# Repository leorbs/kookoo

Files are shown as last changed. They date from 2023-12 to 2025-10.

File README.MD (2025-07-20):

## KOOKOO
~~Very simple~~ script to control a Cuckoo, multiple sensors and sound playback.

## Connecting
Most of the cables have color codes at the end. If you are unsure, read 
the schematics or board layout.

## Compiling

Follow the instructions in the script.ino. When compiling, choose the old bootloader
for the arduino nano:

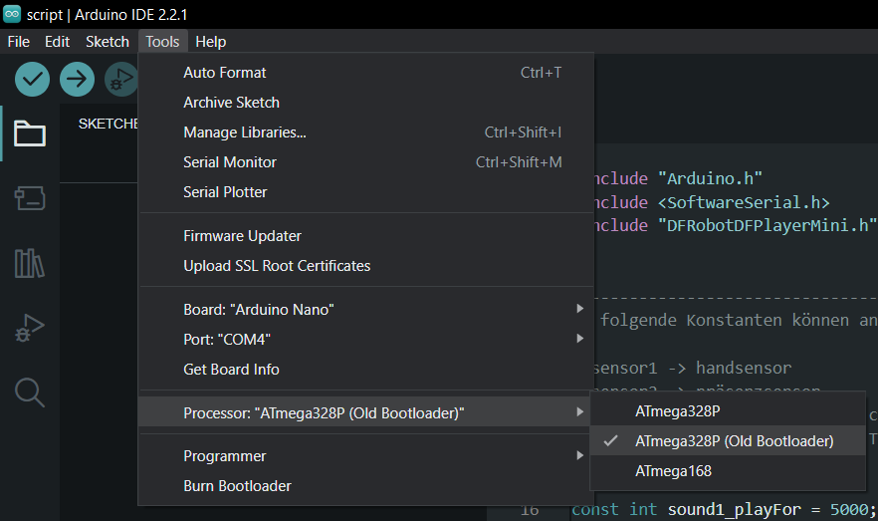
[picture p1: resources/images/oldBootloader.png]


## How to use the SD card

follow the instructions [here](/resources/folderStructure.MD)

## Troubleshooting

- Hand sensor does not work
  - look inside and observe the leds. The LED of the hand sensor module 
  and the LED of the Arduino should light up, when something is near the sensor 
    -  if there is no change on the LEDs then you can try to 
    lower the sensitivity of the sensor module. Look into the guide of
    the sensor module
    - there might be too much sunlight hitting the IR sensor. Try blocking the 
    sunlight and test if the sensor works again
- Shake logic to sensitive
  - adjust values in code
    - SHAKE_SENSITIVITY
    - SHAKE_PICKUP_SPEED
    - SHAKE_OBSERVATION_WINDOW

## PCB Layout
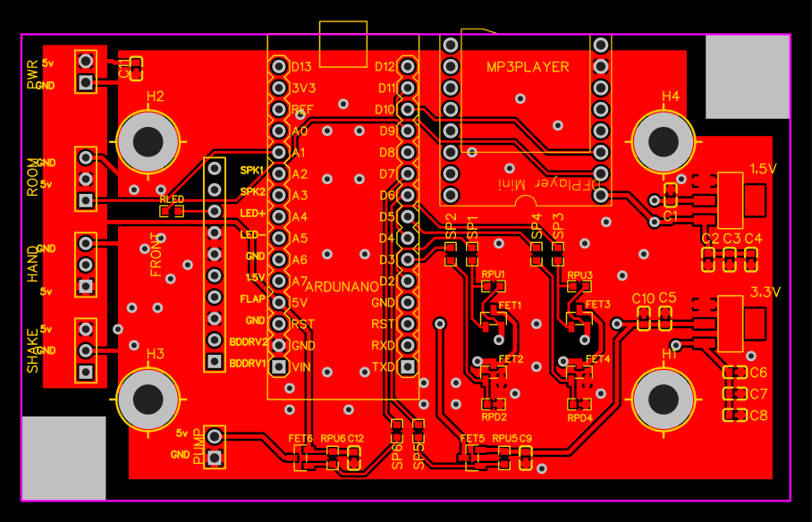
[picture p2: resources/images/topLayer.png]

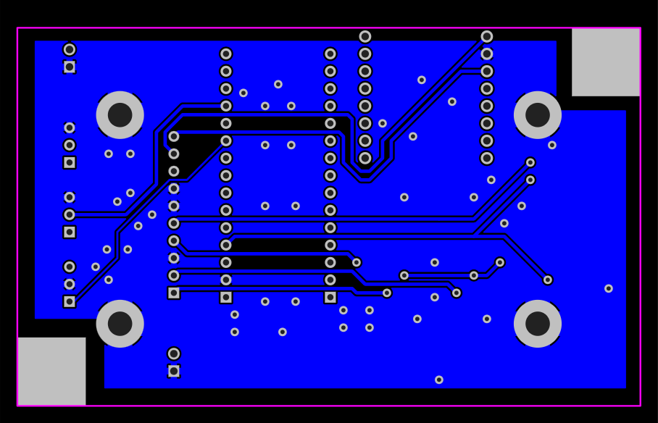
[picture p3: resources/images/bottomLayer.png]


### PCB Schematic

*Mandatory* needs to be fixed directly on the PCB (for now).

- change the resistor if you want a brighter LED
- add a schotty diode to the flap

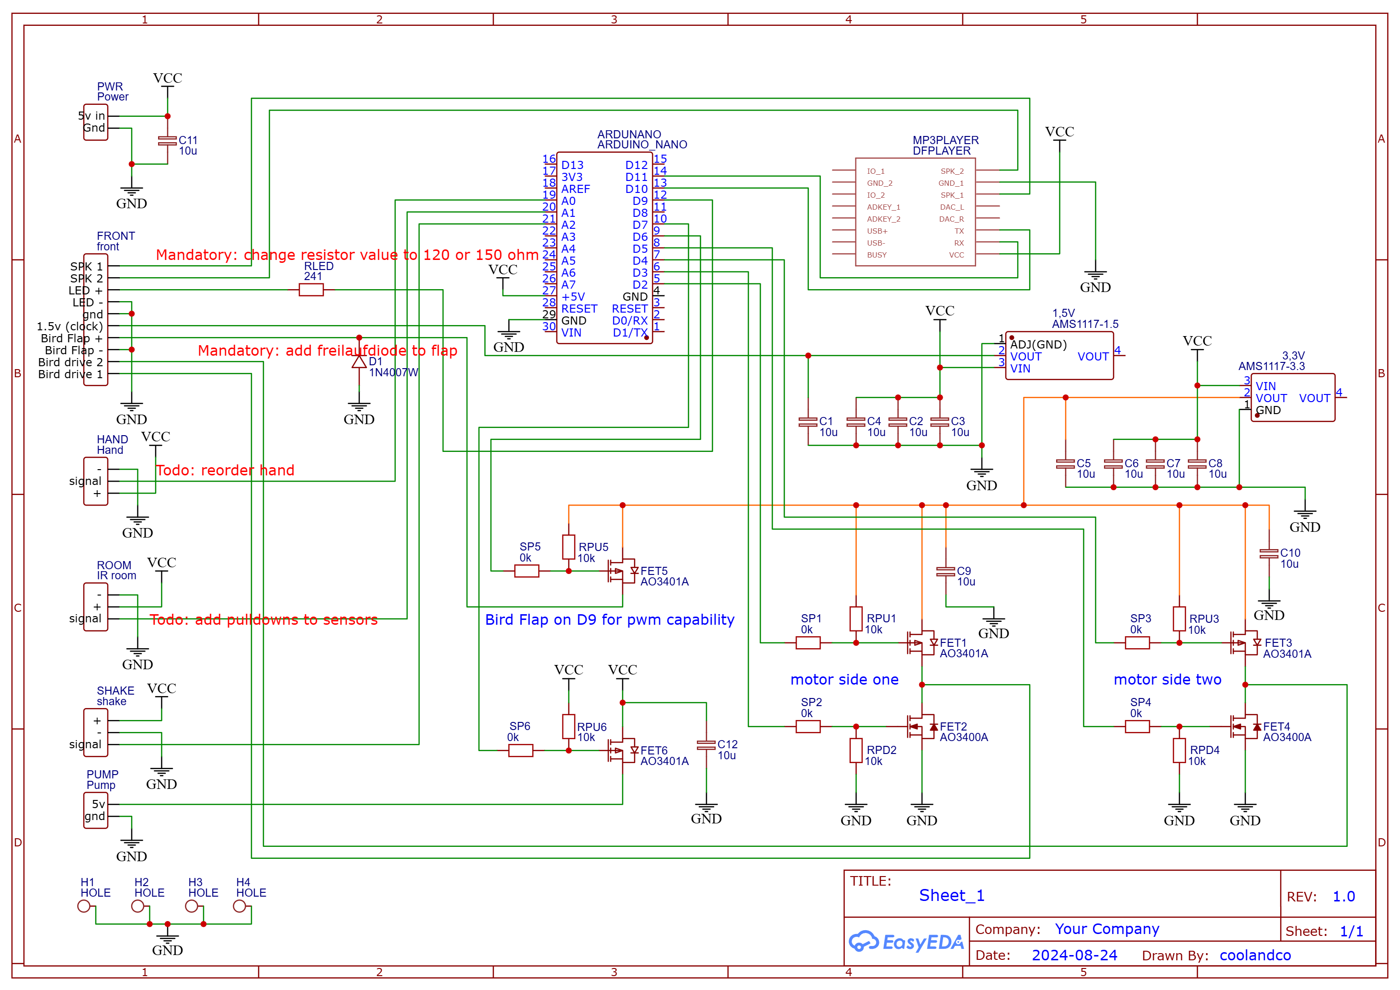
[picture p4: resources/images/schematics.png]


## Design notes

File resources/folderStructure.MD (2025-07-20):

##
Format the MicroUSB in Fat32, standard allocation.
Partitioning table should be in MBR (to be verified).
## Files

Use only files with codecs that the DFPlayer Chip can play. 

One known working solution is the following:
- Open Audacity and mark a section you want to export.
- Press STRG + Shift + E (Export Audio)
  - Format: WAV (Microsoft)
  - Channels: Mono
  - Sample Rate: 44100Hz
  - Encoding: Signed 16-bit PCM
- Export Range: current section
- Export!

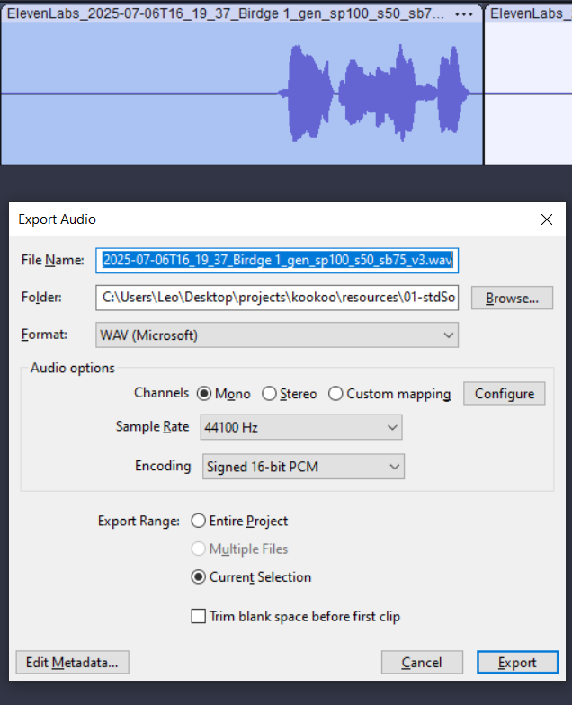
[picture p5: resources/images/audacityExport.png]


## Folder Structure

Example folder names: 
- ``03/001.mp3``
- ``03/002.mp3``
- ``03/003.mp3``
- ``04/001.mp3``

Folder name: only two digits ``01`` - ``13``

File name: three digits + ending e.g.: ``001.wav``. The ending can be wav or mp3.

If a folder is not used anymore, delete that folder (no empty folders)!
If you see a ``System Volume Information`` folder, dont bother, it can stay.

### Folder meaning:
- 01
  - Kookoo standard bird sound(s)
- 02
  - shake sensor activated sounds
- 03
  - one file: 001.wav
  - for the menu beep
- 04 - 13
  - 'someone comes into the room' sounds
  - press the button to iterate through these folders
  - one beep -> folder 04
  - two beeps -> folder 05
  - ...

## Note to the code developer: How does the detection of files work?
Detection of folders works by calling ``mp3Player.readFolderCounts();`` several times
and comparing if the results are the same for multiple consecutive times.
The chip detects folders with files in them.

Detection of files work by playing the first file from a folder and then asking the
chip to return the amount of files from that Folder ``mp3Player.readFileCountsInFolder(i);``.
The amount of files is requested multiple times and after multiple consecutive same answers
it is taken as correct.

Somehow this reliably works. I dont know why...

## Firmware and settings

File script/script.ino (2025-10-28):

#include "Arduino.h"
#include "SoftwareSerial.h"
#include "DFRobotDFPlayerMini.h"
#include "JobManager.cpp"
#include "TimeBasedCounter.cpp"
#include "BirdFlapGenerator.h"
#include "Bounce2.h"

//----------------------------------------
//Install the following libraries from your arduino library manager
//https://github.com/thomasfredericks/Bounce2
//https://github.com/end2endzone/SoftTimers

// use the old bootloader for arduino nano when compiling


// uncomment this line, if you want to show logs on serial:

// #define DEBUG
//----------------------------------------
// Settings

#define VOLUME 23                         // sound volume 0-30

#define SHAKE_SENSITIVITY 20              // up to 1024. The higher the number, the lower the sensitivity
#define SHAKE_PICKUP_SPEED 150            // minimum time in ms between shake incidents to get registered
#define SHAKE_OBSERVATION_WINDOW 4000     // Window to observe shakes in ms
#define COUNTER_SIZE 3                    // how many times should the sensor detect a shake within the window 
#define SHAKE_DETECTION_TIMEOUT 10000     // how much time after the last shake execution (Pfoten weg) before the shake sensor is active again (ms)?

#define ROOM_DETECTION_TIMEOUT 60000      // how much time after the last activity before the room sensor is active (ms)?


#define LED1_BRIGHTNESS 255      // 0-255 led from the front header (big connector)
#define LED2_BRIGHTNESS 255      // 0-255  

#define SOAP_AMOUNT 350          // How long is the Pump on (ms)?
#define LED_BLINKING_SPEED 500   // How long is the LED on/off (ms), Blinking speed.


//----------------------------------------
// internals

#define MAIN_LOOP_TIME_BASE_MS	5

#define HAND_PIN A0            // connect IR hand sensor module to Arduino pin A0
#define ROOM_PIN A1            // praesense sensor module to Arduino pin A1
#define SHAKE_PIN A2           // sensor module for tamper detection to Arduino pin A2

#define RNG_SEED_PIN A6        // Used to initialize the randomnes

#define BUTTON_1 12            // Button for setting the folder
#define BUTTON_2 A3            // Button for setting the folder
#define BUTTON_3 A5            // Button for manual soap

#define LED1_PIN 9             // D9 LED
#define LED2_PIN A4            // LED2
#define PUMP_PIN 7             // D7 soap pump

#define BIRD_FLAP_PIN 6        // D6 bird flap

#define BIRD_MOTOR1_GND_PIN 5  // D5 
#define BIRD_MOTOR1_VCC_PIN 2  // D2

#define BIRD_MOTOR2_GND_PIN 3  // D3 
#define BIRD_MOTOR2_VCC_PIN 4  // D4

#define DFPLAYER_RX_PIN 10     // D10 -> RX on Arduino TX on DFPlayer
#define DFPLAYER_TX_PIN 11     // D11 -> TX on Arduino RX on DFPlayer



#ifdef DEBUG
  #warning "Serial debugging is enable. This will slow down program flow"
#endif


// DFPlayer maintenance timers
unsigned long lastDFPlayerReset = 0;
unsigned long lastSoapUse = 0;

// Intervals
const unsigned long DFPLAYER_RESET_INTERVAL = 10UL * 24UL * 60UL * 60UL * 1000UL; // 10 days
const unsigned long INACTIVITY_WINDOW = 3UL * 60UL * 60UL * 1000UL;               // 3 hours

SoftwareSerial DFPlayerSoftwareSerial(DFPLAYER_RX_PIN,DFPLAYER_TX_PIN);// RX, TX
DFRobotDFPlayerMini mp3Player;
SoftTimer mainLoopTimer;

#define FOLDER_STANDARD_BIRD_SOUND 1
#define FOLDER_SHAKE_SENSOR_ACTIVATED 2
#define FOLDER_BEEP 3
#define FOLDER_ROOM_START 4
#define FOLDER_ROOM_END 13

uint8_t maxDetectedFolders = FOLDER_ROOM_END;
uint8_t folderFileCounts[FOLDER_ROOM_END + 1]; // Index 1-13 used
uint8_t currentRoomFolder = FOLDER_ROOM_START;
uint8_t currentRoomFolder_beepCyclePosition = 0;

Bounce2::Button button1 = Bounce2::Button();
Bounce2::Button button2 = Bounce2::Button();
Bounce2::Button button3 = Bounce2::Button();


TimeBasedCounter timeBasedCounter(SHAKE_OBSERVATION_WINDOW);
unsigned long currentTime = 0;

void soundOn();
void soundOff();
void flapStart();
void flapEnd();
void birdOutStart();
void birdOutEnd();
void birdInStart();
void birdInEnd();
void flapBreakStart();
void flapBreakEnd();
void soapOn();
void soapOff();
void roomOn();
void roomOff();
void shakeOn();
void shakeOff();
void ledOnStart();
void ledOnEnd();
void ledOffStart();
void ledOffEnd();
void doMp3PlayerSetupStuff();

const uint16_t flapBreakPattern_single[] = {200, 600};
const uint16_t flapPattern_single[] =        {500};

SoundParams soundParams;

int flapPattern_currentIndex = 0;
int flapBreakPattern_currentIndex = 0;

JobManager sound(15000, 800, soundOn, soundOff, false, false); //backoff is the safety time for bird termination

JobManager flap(500, flapStart, flapEnd);
JobManager flapBreak(200, flapBreakStart, flapBreakEnd);
JobManager birdOut(240, birdOutStart, birdOutEnd);
JobManager birdIn(260, birdInStart, birdInEnd);

JobManager soap(SOAP_AMOUNT, 2000, soapOn, soapOff, true, true);
JobManager room(500, ROOM_DETECTION_TIMEOUT, roomOn, roomOff, true, true);
JobManager shake(550, 10000, shakeOn, shakeOff, false, true);

// only sound will control bird
// bird can only come out with sound
// that means if one sound is running, there can be no other sound and therefore no other bird
// sound execution time -> full bird cycle. Execution time mandatory to prevent double bird scenario

JobManager ledOn(LED_BLINKING_SPEED, ledOnStart, ledOnEnd);
JobManager ledOff(LED_BLINKING_SPEED, ledOffStart, ledOffEnd);


void soapOn() {
  Serial.println(F("switch soap on"));
  digitalWrite(PUMP_PIN, LOW);

  // set new sound params for the sound job
  Serial.print(sound.isJobActive());
  Serial.println(F(" = Sound job currently active"));

  if(!sound.isJobActive()) {

    soundParams.folderId = FOLDER_STANDARD_BIRD_SOUND;
    soundParams.triggerBird = true;
    Serial.print(F(" setting soundParams.flapBreakPattern. flapBreakPattern_single[0]: "));
    Serial.println(flapBreakPattern_single[0]);
    soundParams.flapBreakPattern = flapBreakPattern_single;
    soundParams.flapPattern = flapPattern_single;
    soundParams.flapBreakPatternSize = 2;
    soundParams.flapPatternSize = 1;

    sound.startJob();
  }

}

void soapOff() {
  Serial.println(F("switch soap off"));
  digitalWrite(PUMP_PIN, HIGH);
}

void roomOn() {

  Serial.println(F("room On"));

  if(!sound.isJobActive()) {
    //execute the chain
    generateSpeechLikeFlappingPattern(soundParams);
    soundParams.folderId = currentRoomFolder;
    soundParams.triggerBird = true;

    sound.startJob();
  }
}

void roomOff() {
}

void shakeOn() {
  Serial.println(F("shake On"));
  if(!sound.isJobActive()) {

    // flaps get ignored because trigger bird is false
    soundParams.folderId = FOLDER_SHAKE_SENSOR_ACTIVATED;
    soundParams.triggerBird = false;
    soundParams.flapBreakPattern = flapBreakPattern_single;
    soundParams.flapPattern = flapPattern_single;
    soundParams.flapBreakPatternSize = 2;
    soundParams.flapPatternSize = 1;

    //execute the chain
    sound.startJob();
  }
}

void shakeOff() {
}

void soundOn() {

  Serial.println(F("sound on."));
  Serial.print(soundParams.folderId);
  Serial.println(F(" folderId playing"));

  
  int count = folderFileCounts[soundParams.folderId];
  uint8_t fileNum = random(1, count + 1);
  Serial.print(F("Playing file "));
  Serial.print(fileNum);
  Serial.print(F(" from folder "));
  Serial.println(soundParams.folderId);
  mp3Player.playFolder(soundParams.folderId, fileNum);

  if(soundParams.triggerBird) {
    Serial.println(F("Sound doing Birdstuff"));

    // 15 Seconds max sound lengh for safety
    // some other routine should test if mp3 is still playing and  stop sound job (and therefore pull in bird)
    sound.setNewDurationTime(15000);
    sound.restartJobTimer();

    flapPattern_currentIndex = 0;
    flapBreakPattern_currentIndex = 0;

    //execute the bird chain
    birdOut.startJob();
  }

}

void soundOff() {
}

void birdOutStart() {
  Serial.println(F("Bird out start"));
  digitalWrite(BIRD_MOTOR1_GND_PIN, HIGH);
  digitalWrite(BIRD_MOTOR1_VCC_PIN, LOW);
}

void birdOutEnd() {
  Serial.println(F("Bird out end"));
  digitalWrite(BIRD_MOTOR1_GND_PIN, LOW);
  digitalWrite(BIRD_MOTOR1_VCC_PIN, HIGH);
  
  //execute the chain
  if(soundParams.flapBreakPatternSize > soundParams.flapPatternSize) {
    flapBreak.startJob();
  } else {
    flap.startJob();
  }

}

void birdInStart() {
  Serial.println(F("Bird in start"));
  digitalWrite(BIRD_MOTOR2_GND_PIN, HIGH);
  digitalWrite(BIRD_MOTOR2_VCC_PIN, LOW);

}

void birdInEnd() {
  Serial.println(F("Bird in end"));
  digitalWrite(BIRD_MOTOR2_GND_PIN, LOW);
  digitalWrite(BIRD_MOTOR2_VCC_PIN, HIGH);
}


// ========================================================================================================================

void flapStart() {
  Serial.print(F("flap Start"));
  Serial.println(soundParams.flapPattern[flapPattern_currentIndex]);

  digitalWrite(BIRD_FLAP_PIN, LOW);

  flap.setNewDurationTime(soundParams.flapPattern[flapPattern_currentIndex]);
  flap.restartJobTimer();
}

void flapEnd() {
  Serial.println(F("flap End"));
  digitalWrite(BIRD_FLAP_PIN, HIGH);

  flapPattern_currentIndex = flapPattern_currentIndex + 1;

  //check flap break possible
  if(flapBreakPattern_currentIndex < soundParams.flapBreakPatternSize && sound.isJobActive()) {
    flapBreak.startJob();
  } else {
    //no flap break anymore (or sound got ended). Do now bird in
    birdIn.startJob();
  }

}

void flapBreakStart(){
  Serial.print(F("flapBreakStart "));
  Serial.println(soundParams.flapBreakPattern[flapBreakPattern_currentIndex]);

  flapBreak.setNewDurationTime(soundParams.flapBreakPattern[flapBreakPattern_currentIndex]);
  flapBreak.restartJobTimer();

}

void flapBreakEnd() {
  Serial.println(F("flapBreakEnd"));

  flapBreakPattern_currentIndex = flapBreakPattern_currentIndex + 1;


  //check flap possible
  if(flapPattern_currentIndex < soundParams.flapPatternSize && sound.isJobActive()) {
    flap.startJob();
  } else {
    //no flap anymore (or sound got ended). Do now bird in
    birdIn.startJob();
  }

}

// ========================================================================================================================
void printDetail(uint8_t type, int value){
  switch (type) {
    case TimeOut:
      Serial.println(F("DFPLAYER: Time Out!"));
      break;
    case WrongStack:
      Serial.println(F("DFPLAYER: Stack Wrong!"));
      break;
    case DFPlayerCardInserted:
      Serial.println(F("DFPLAYER: Card Inserted!"));
      break;
    case DFPlayerCardRemoved:
      Serial.println(F("DFPLAYER: Card Removed!"));
      break;
    case DFPlayerCardOnline:
      Serial.println(F("DFPLAYER: Card Online!"));
      break;
    case DFPlayerUSBInserted:
      Serial.println(F("DFPLAYER: USB Inserted!"));
      break;
    case DFPlayerUSBRemoved:
      Serial.println(F("DFPLAYER: USB Removed!"));
      break;
    case DFPlayerPlayFinished:
      Serial.print(F("DFPLAYER: Number: "));
      Serial.print(value);
      Serial.println(F(" Play Finished!"));
      break;
    case DFPlayerError:
      Serial.print(F("DFPLAYER: DFPlayerError:"));
      switch (value) {
        case Busy:
          Serial.println(F("DFPLAYER: Card not found"));
          break;
        case Sleeping:
          Serial.println(F("DFPLAYER: Sleeping"));
          break;
        case SerialWrongStack:
          Serial.println(F("DFPLAYER: Get Wrong Stack"));
          break;
        case CheckSumNotMatch:
          Serial.println(F("DFPLAYER: Check Sum Not Match"));
          break;
        case FileIndexOut:
          Serial.println(F("DFPLAYER: File Index Out of Bound"));
          break;
        case FileMismatch:
          Serial.println(F("DFPLAYER: Cannot Find File"));
          break;
        case Advertise:
          Serial.println(F("DFPLAYER: In Advertise"));
          break;
        default:
          break;
      }
      break;
    default:
      break;
  }
}

void setup() {
  mainLoopTimer.setTimeOutTime(MAIN_LOOP_TIME_BASE_MS);
  mainLoopTimer.reset();

  pinMode(HAND_PIN, INPUT_PULLUP);
  pinMode(ROOM_PIN, INPUT_PULLUP);
  pinMode(SHAKE_PIN, INPUT);

  pinMode(LED_BUILTIN, OUTPUT);
  pinMode(LED1_PIN, OUTPUT);

  pinMode(PUMP_PIN, OUTPUT);
  digitalWrite(PUMP_PIN, HIGH);

  pinMode(BIRD_FLAP_PIN, OUTPUT);
  digitalWrite(BIRD_FLAP_PIN, HIGH);

  pinMode(BIRD_MOTOR1_GND_PIN, OUTPUT);
  digitalWrite(BIRD_MOTOR1_GND_PIN, LOW);
  pinMode(BIRD_MOTOR1_VCC_PIN, OUTPUT);
  digitalWrite(BIRD_MOTOR1_VCC_PIN, HIGH);
  pinMode(BIRD_MOTOR2_GND_PIN, OUTPUT);
  digitalWrite(BIRD_MOTOR2_GND_PIN, LOW);
  pinMode(BIRD_MOTOR2_VCC_PIN, OUTPUT);
  digitalWrite(BIRD_MOTOR2_VCC_PIN, HIGH); 

  button1.attach ( BUTTON_1 , INPUT_PULLUP );
  button1.interval( 10 );
  button1.setPressedState( LOW );

  button2.attach ( BUTTON_2 , INPUT_PULLUP );
  button2.interval( 10 );
  button2.setPressedState( LOW );

  button3.attach ( BUTTON_3 , INPUT_PULLUP );
  button3.interval( 10 );
  button3.setPressedState( LOW );


  #ifdef DEBUG
    Serial.begin(9600);
  #endif

  int seed = analogRead(RNG_SEED_PIN);

  Serial.print(F("seed is: "));
  Serial.println(seed);

  //initialize randomness so it is not every time the same
  randomSeed(seed);



  //mp3 player stuff
  DFPlayerSoftwareSerial.begin(9600); // DFPlayer Mini mit SoftwareSerial initialisieren
  bool mp3PlayerOnline = mp3Player.begin(DFPlayerSoftwareSerial, true, true);
  
  if(mp3PlayerOnline) {
    doMp3PlayerSetupStuff();
  }


  ledOn.startJob();
}

void doMp3PlayerSetupStuff() {
  mp3Player.setTimeOut(2000);
  mp3Player.volume(0);
  delay(50);

  int consecutiveSame = 0;
  int lastValue = INT16_MAX;
  int currentRead;
  bool filedetection = false;


  while(consecutiveSame < 4) {
    Serial.print(F("consecutiveSame: "));
    Serial.println(consecutiveSame);
    currentRead = mp3Player.readFolderCounts();

    if(mp3Player.available() ) {
        uint8_t type = mp3Player.readType();
        int value = mp3Player.read();
        printDetail(type, value);
    }
    Serial.print(F("currentRead: "));
    Serial.println(currentRead);
    if(lastValue == currentRead){
      consecutiveSame += 1;
    } else {
      consecutiveSame = 0;
      lastValue = currentRead;
    }
  }

  maxDetectedFolders = lastValue;
  Serial.print(F("maxDetectedFolders after readFolderCounts "));
  Serial.println(maxDetectedFolders);

  if(maxDetectedFolders > FOLDER_ROOM_END || maxDetectedFolders < 0) {

    Serial.print(F("Getting folder count is not supported or errornous. Falling back to file detection "));
    filedetection = true;

    maxDetectedFolders = FOLDER_ROOM_END; //setting temporary for iterating over folders (this is not good code, I know, sry)
  }

  for (int i = 1; i <= maxDetectedFolders; i++) {
    mp3Player.playFolder(i, 1);
    delay(100);

    lastValue = INT16_MAX;
    consecutiveSame = 0;
    while(consecutiveSame < 6) {
      Serial.print(F("consecutiveSame: "));
      Serial.println(consecutiveSame);
      currentRead = mp3Player.readFileCountsInFolder(i);
      
      if(mp3Player.available() ) {
        uint8_t type = mp3Player.readType();
        int value = mp3Player.read();
        printDetail(type, value);
      }

      delay(50);
      Serial.print(F("currentRead: "));
      Serial.println(currentRead);
      if(lastValue == currentRead){
        consecutiveSame += 1;
      } else {
        consecutiveSame = 0;
        lastValue = currentRead;
      }
    }

    // mp3Player.playFolder(i, lastValue);
    // delay(100);
    // currentRead = mp3Player.readFileCountsInFolder(i);
    // Serial.print(F("lastValue currentRead: "));
    // Serial.println(currentRead);

    folderFileCounts[i] = lastValue;

    Serial.print(F("folderFileCounts[i] i: "));
    Serial.print(i);
    Serial.print(F(" folderFileCounts: "));
    Serial.println(lastValue);

    if(lastValue == 0) {
      Serial.println(F("Found a Folder with 0 files. Aborting... "));
      break;
    } else if (lastValue == -1) {
      Serial.println(F("Found a Folder with -1 files. Aborting... "));
      break;
    }
  }


  if(filedetection) {
    Serial.println(F("Filedetection is active."));
    maxDetectedFolders = 0;

    for(int i = 1; i <= FOLDER_ROOM_END; i++) {
      if(folderFileCounts[i] > 0 && folderFileCounts[i] < 255) {
        maxDetectedFolders = maxDetectedFolders + 1;
      } else {
        //abort when there is a folder detected with 0 files
        break;
      }
    }

    Serial.print(F("Detected files in the first X folders: "));
    Serial.println(maxDetectedFolders);

    if(maxDetectedFolders > FOLDER_ROOM_END) {
      //safety
      maxDetectedFolders = FOLDER_ROOM_END;
      Serial.println(F("Safety for filedetection activated"));
    }
  }


  mp3Player.stop();
  delay(500);

  mp3Player.volume(VOLUME);
  mp3Player.setTimeOut(1000);
}

void reinitializeDFPlayerSerial() {

  mp3Player.stop();
  delay(200);

  DFPlayerSoftwareSerial.end();
  delay(100);

  DFPlayerSoftwareSerial.begin(9600);
  delay(200);

  bool ok = mp3Player.begin(DFPlayerSoftwareSerial, true, true);

  Serial.println(F("Reinitialized MP3 Player"));
  if (ok) {
  Serial.println(F("initialization was ok"));
    mp3Player.volume(VOLUME);
  }
  
}


void loop() {
  while(!mainLoopTimer.hasTimedOut());
  mainLoopTimer.reset();
  
  currentTime = millis();

  // Sensor-Zustand überprüfen
  bool handSensor_isOn = !digitalRead(HAND_PIN);
  bool roomSensor_isOn = digitalRead(ROOM_PIN);
  uint16_t shakeSensor_value = analogRead(SHAKE_PIN);

  //display sensor1 state with buldin led
  digitalWrite(LED_BUILTIN, handSensor_isOn);

  button1.update();
  button2.update();
  button3.update();

  soap.handleJob();
  room.handleJob();
  shake.handleJob();
  sound.handleJob();
  birdOut.handleJob();
  birdIn.handleJob();
  flap.handleJob();
  flapBreak.handleJob();
  ledOn.handleJob();
  ledOff.handleJob();


  //--------------------------------------
  // sound observation loop

  if(mp3Player.available() ) {

    uint8_t type = mp3Player.readType();
    int value = mp3Player.read();


    if (sound.isJobActive() && type == DFPlayerPlayFinished) {
    //sound is done playing. Terminate Bird.
      Serial.print(F("DFPLAYER: Finished playing filenumber "));
      Serial.println(value);
      mp3Player.stop();
      sound.endJob(); //terminates bird
    } else {
      printDetail(type, value); //Print the detail message from DFPlayer to handle different errors and states.
    }
  }


  //--------------------------------------
  if (handSensor_isOn) {
    soap.startJob();
    lastSoapUse = currentTime;
    timeBasedCounter.reset(); //shake is allowed when there is normal usage
    room.renewBackoff(); // when someone uses the soap, we dont need to execute the room procedure
  } else {
    soap.resetRunOnce(); // this prevents continuous soap, if the handsensor is continuously on
  }

  if (roomSensor_isOn) {
    room.startJob();
    room.renewBackoff(); // this renewes the backoff when someone is constantly in the room. The "room experience" is only for when you enter the room
  } else {
    room.resetRunOnce();
  }

  //--------------------------------------
  // Periodic DFPlayer serial reinitialization (rollover-safe)
  if ((unsigned long)(currentTime - lastDFPlayerReset) >= DFPLAYER_RESET_INTERVAL &&
      (unsigned long)(currentTime - lastSoapUse) >= INACTIVITY_WINDOW) {

    Serial.println(F("Reinitializing DFPlayer serial interface after long uptime + inactivity..."));
    reinitializeDFPlayerSerial();

    lastDFPlayerReset = currentTime;  // Update timestamp safely
  }


  // ======================================
  // new idea:
  // add the analog signal to a counter
  // decrease counter in each loop
  // if counter too high, then tilt

  if(shakeSensor_value > SHAKE_SENSITIVITY && currentTime - timeBasedCounter.getLatestTime() > SHAKE_PICKUP_SPEED && !shake.isBackoffActive()) {

    bool wereThereMultipleShakeIncidents = timeBasedCounter.addTimeAndCheck(currentTime);

#ifdef DEBUG
    Serial.println(F("================"));
    Serial.print(wereThereMultipleShakeIncidents);
    Serial.println(F(" = wereThereMultipleShakeIncidents"));
    Serial.print(timeBasedCounter.getLatestTime());
    Serial.println(F(" = latest time"));
    Serial.print(currentTime);
    Serial.println(F(" = current time"));

    Serial.print(F("shake detected: shake value "));
    Serial.println(shakeSensor_value);
    Serial.print(timeBasedCounter.getCurrentShakeCounter(currentTime));
    Serial.println(F(" is the current shakes detected"));
    Serial.println(F("================"));
#endif

    if(wereThereMultipleShakeIncidents) {
      shake.startJob();
    }
  }


  // ======================================
  // WARNING, THIS BLOCKS THE LOOP FLOW
  if ( button1.pressed() || button2.pressed() ) {
    
    Serial.println(F("button1 pressed"));
    currentRoomFolder = currentRoomFolder + 1;

    Serial.print(F("currentRoomFolder"));
    Serial.println(currentRoomFolder);

    
    Serial.print(F("maxDetectedFolders"));
    Serial.println(maxDetectedFolders);

    if(currentRoomFolder > maxDetectedFolders) {
      currentRoomFolder = (uint8_t) FOLDER_ROOM_START;
    }

    Serial.print(F("sounds will be played from room "));
    Serial.println(currentRoomFolder);

    for(uint8_t i = FOLDER_ROOM_START; i <= currentRoomFolder; i++) {
      mp3Player.playFolder(FOLDER_BEEP, 1);
      delay(600);
    }
    mp3Player.stop();

  }


  //pump manual override
  if(button3.pressed()) {
    Serial.println(F("Manual soap on "));
    digitalWrite(PUMP_PIN, LOW);
  } else if(button3.released()) {
    Serial.println(F("manual soap off"));
    digitalWrite(PUMP_PIN, HIGH);
  }

}


void ledOnStart() {
  // Serial.println(F("LED on"));
  analogWrite(LED1_PIN, LED1_BRIGHTNESS);
  analogWrite(LED2_PIN, LED2_BRIGHTNESS);
}
void ledOnEnd() {
  ledOff.startJob();
}
void ledOffStart() {
  // Serial.println(F("LED off"));
  digitalWrite(LED1_PIN, LOW);
  digitalWrite(LED2_PIN, LOW);
}
void ledOffEnd() {
  ledOn.startJob();
}

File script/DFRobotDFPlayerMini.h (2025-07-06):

/*!
 * @file DFRobotDFPlayerMini.h
 * @brief Optimized DFPlayer Mini MP3 module driver (Replacement for DFRobotDFPlayerMini library)
 * 
 * This library provides a reliable interface to the DFPlayer Mini module, maintaining 
 * compatibility with the original DFRobotDFPlayerMini API. It supports Arduino, ESP8266, 
 * and ESP32 boards using hardware or software serial at 9600 baud.
 * 
 * Improvements:
 *  - Robust parsing of incoming serial data with frame validation (start byte, length, checksum, end byte).
 *  - Safe, non-blocking waits with timeouts to prevent watchdog resets (especially on ESP8266/ESP32).
 *  - Optional debug logging for sent/received data, enabled via DFPLAYER_DEBUG macro.
 *  - Thread-safe and reentrant design for multiple instances (each instance manages its own serial stream).
 * 
 * The class and constants remain identical to the original library for drop-in replacement.
 * 
 * © 2024 Original by DFRobot, Optimized version by 99buntai. Licensed under MIT License.
 */

#ifndef DFRobotDFPlayerMini_h
#define DFRobotDFPlayerMini_h

#include <Arduino.h>

// Equalizer presets
#define DFPLAYER_EQ_NORMAL 0
#define DFPLAYER_EQ_POP 1
#define DFPLAYER_EQ_ROCK 2
#define DFPLAYER_EQ_JAZZ 3
#define DFPLAYER_EQ_CLASSIC 4
#define DFPLAYER_EQ_BASS 5

// Playback devices
#define DFPLAYER_DEVICE_U_DISK 1
#define DFPLAYER_DEVICE_SD 2
#define DFPLAYER_DEVICE_AUX 3    // not used by DFPlayer Mini
#define DFPLAYER_DEVICE_SLEEP 4  // enters sleep mode
#define DFPLAYER_DEVICE_FLASH 5

// Frame lengths
#define DFPLAYER_RECEIVED_LENGTH 10   // length of incoming frame
#define DFPLAYER_SEND_LENGTH 10       // length of outgoing frame

// Enable debug logging by defining DFPLAYER_DEBUG (e.g., via build flags or before including this header)
//#define DFPLAYER_DEBUG

// Player return types (for readType())
#define TimeOut 0               // Timeout or no response
#define WrongStack 1            // Malformed or unexpected frame
#define DFPlayerCardInserted 2
#define DFPlayerCardRemoved 3
#define DFPlayerCardOnline 4
#define DFPlayerPlayFinished 5
#define DFPlayerError 6
#define DFPlayerUSBInserted 7
#define DFPlayerUSBRemoved 8
#define DFPlayerUSBOnline 9
#define DFPlayerCardUSBOnline 10
#define DFPlayerFeedBack 11     // Generic feedback for query commands

// Error codes (for DFPlayerError type's parameter via read())
#define Busy 1           // Module is busy (e.g., initializing or reading)
#define Sleeping 2       // Module is in sleep mode
#define SerialWrongStack 3  // Incorrect serial data received
#define CheckSumNotMatch 4  // Checksum validation failed
#define FileIndexOut 5    // File index out of bounds
#define FileMismatch 6    // File unable to play (mismatch or unsupported)
#define Advertise 7       // In advertising (ADVERT) mode, cannot execute command

#define Stack_Header      0
#define Stack_Version     1
#define Stack_Length      2
#define Stack_Command     3
#define Stack_ACK         4
#define Stack_Parameter   5
#define Stack_CheckSum    7
#define Stack_End         9

class DFRobotDFPlayerMini {
public:
    DFRobotDFPlayerMini() : 
        _serial(nullptr), _timeOutDuration(500), _receivedIndex(0),
        _isAvailable(false), _isSending(false),
        _handleType(0), _handleCommand(0), _handleParameter(0) {
        // Prepare the static part of the send buffer (start, version, length, end)
        _sending[0] = 0x7E;    // Start byte
        _sending[1] = 0xFF;    // Version (fixed)
        _sending[2] = 0x06;    // Length (fixed)
        _sending[3] = 0x00;    // Command will be filled in on send
        _sending[4] = 0x00;    // ACK flag (0 or 1) will be set in begin()
        _sending[5] = 0x00;    // Parameter high byte (filled as needed)
        _sending[6] = 0x00;    // Parameter low byte  (filled as needed)
        // [7] and [8] will hold checksum, [9] is end byte (0xEF)
        _sending[7] = 0x00;
        _sending[8] = 0x00;
        _sending[9] = 0xEF;    // End byte
    }

    // Initialize the DFPlayer module. 
    // stream: the serial stream (HardwareSerial or SoftwareSerial) already begun at 9600 baud.
    // isACK: true to enable command acknowledgements (default), false to disable ACK for faster/non-blocking operation.
    // doReset: true to send a reset command to DFPlayer on begin (recommended to initialize module).
    bool begin(Stream &stream, bool isACK = true, bool doReset = true);

    // Check if the DFPlayer has sent any message (track end, feedback, error, etc.).
    // Returns true if a new event is available to read via readType() and read().
    bool available();

    // Wait for an event to be available or until timeout (in milliseconds).
    // If duration is 0, uses the default _timeOutDuration. Returns true if an event arrived, false if timed out.
    bool waitAvailable(unsigned long duration = 0);

    // Get the type of the last received message (one of the DFPlayer... constants above, e.g., DFPlayerPlayFinished, DFPlayerError, etc.).
    uint8_t readType();

    // Get the parameter of the last received message (e.g., track number for DFPlayerPlayFinished, error code for DFPlayerError, etc.).
    uint16_t read();

    // Get the last received command byte from the DFPlayer (for low-level use or debugging).
    uint8_t readCommand();

    // Set the serial communication timeout duration (milliseconds). Default is 500ms.
    void setTimeOut(unsigned long timeOutDuration);
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

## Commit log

2023-12-10 Add 2nd relay. Remove startup switching of relays
    [schematics.fzz]
2023-12-10 fixed schematic mistake
    [schematics.fzz]
2024-01-25 Added blinking LED and a 3rd sensor with a 3rd sound
2024-09-14 current state
    [schematics.fzz]
2025-07-31 add second LED. Add second button
2025-08-22 fix timebasedcounter by not resetting to 0 but rather working with shifting them relatively
    [TimeBasedCounter.cpp, script.ino]
2025-08-22 start soap in "used" state, to allow for an active sensor during boot, without triggering the soap
2025-08-27 add manual soap button (for refilling the soap)
2025-10-28 add reset for mp3player
    [script.ino]
